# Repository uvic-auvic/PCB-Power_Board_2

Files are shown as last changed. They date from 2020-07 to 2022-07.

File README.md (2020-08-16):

# Power Board 2

## Overview
The Autonomous Underwater Vehicle Interdisciplinary Club (AUVIC) competes in an annual international competition where teams build autonomous underwater vehicles (AUVs) to complete an underwater obstacle course. AUVIC is in need of a new power and battery management board(PMB) for the 2021 Autonomous Underwater Vehicle (AUV).

## Specifications
The new PMB is divided into four subsections. The requirements for each subsection are outlined in the following sections.

### 3.1	Battery Management
- Should have a input voltage range of 18V to 28V.
- Should use two 6 cell LiPo batteries as its power source.
- Should have the ability to run the two batteries in parallel.
- Each battery should have fuses. Regular sized automotive fuses are recommended.
- Should have LEDs to indicate if the battery is connected.
- Should have the ability to monitor battery pack voltage, individual cell voltage and pack current.

### 3.2	Power Distribution
- Should have the following power outputs for external systems:
  - 5V at 8A.
    - LCD board - 4A*
    - Inertial Measurement Unit (IMU) - 500mA
    - Hydrophones - 250mA*
    - Torpedo 5V electronics - 250mA*
    - Motor controller 5V electronics - 250mA*
    - Buffer for unplanned boards - 2.75A
  - 12V at 8A.
    - Doppler Velocity Log (DVL) - 3A
    - Ball dropper and grabber arm - 3A*
    - Buffer for unplanned boards - 2A
  - 16V at 3A.
    - Nvidia Jetson TX2 and peripherals - 3A
  - VBatt (22.2V nominal) at 60A continuous.
    - Motor controller - 60A peak
    - Torpedo launcher - 30A for < 1s
- Should be able to switch on/off all external power using the microcontroller.
- Should have the ability to monitor current for each external power output.
- Should have LEDs at each output to indicate if the output is on or off.
- Should have fuses at each output. Regular sized automotive fuses are recommended.

\* = Estimated values.

### 3.3	Microcontroller & Communication
- Should use a STM32F413 microcontroller. 
- Should have a RS232 transceiver to communicate with an IMU.
- Should have LEDs connected to the microcontroller for debugging and to show system status.
- Should use a Controller Area Network (CAN) bus to communicate to external systems.

### 3.4	Sensors
- Should connect to a reed switch to power on/off the AUV.
- Should connect to a water sensor to detect leaks in the vehicle’s housing.
- Should measure internal pressure, temperature, and humidity.
- Should connect to an external water pressure sensor used to determine the AUV’s depth in the water.

## Progress
Schematic completed

Simulations completed

Layout in progress

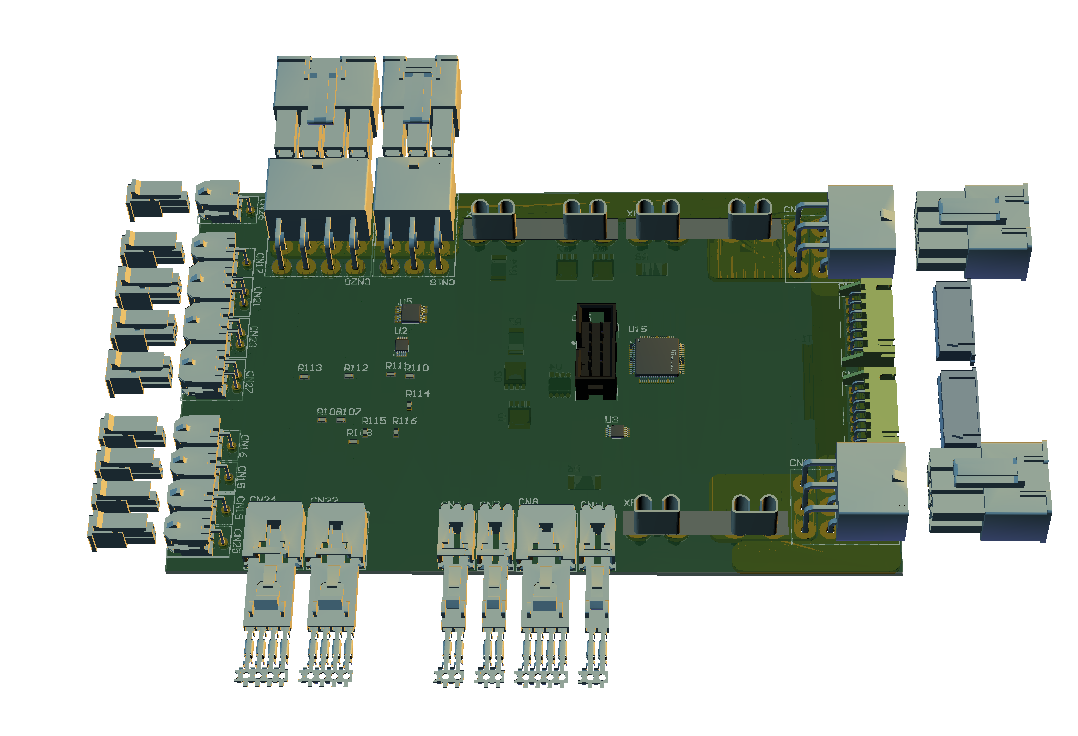
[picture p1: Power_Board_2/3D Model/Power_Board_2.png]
Image of layout thus far


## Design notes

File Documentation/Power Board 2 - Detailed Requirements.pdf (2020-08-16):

## Overview

The Autonomous Underwater Vehicle Interdisciplinary Club (AUVIC) competes in an annual international competition where teams build autonomous underwater vehicles (AUVs) to complete an underwater obstacle course. AUVIC is in need of a new power and battery management board(PMB) for the 2021 Autonomous Underwater Vehicle (AUV).

## Specifications

The new PMB is divided into four subsections. The requirements for each subsection are outlined in the following sections.

## 3.1 Battery Management

The following specifications were established by AUVIC for the battery management section of the power board:
1. Should have a input voltage range of 18V to 28V.
2. Should use two 6 cell LiPo batteries as its power source.
3. Should have the ability to run the two batteries in parallel.
4. Each battery should have fuses. Regular sized automotive fuses are recommended.
5. Should have LEDs to indicate if the battery is connected.
6. Should have the ability to monitor battery pack voltage, individual cell voltage and pack current.

## 3.2 Power Distribution

The following specifications were provided by AUVIC for the power distribution section of the PMB:
1. Should have the following power outputs for external systems:
1.1. 5V at 8A.
1.1.1. LCD board - 4A*
1.1.2. Inertial Measurement Unit (IMU) - 500mA
1.1.3. Hydrophones - 250mA*
1.1.4. Torpedo 5V electronics - 250mA*
1.1.5. Motor controller 5V electronics - 250mA*
1.1.6. Buffer for unplanned boards - 2.75A
1.2. 12V at 8A.
1.2.1. Doppler Velocity Log (DVL) - 3A
1.2.2. Ball dropper and grabber arm - 3A*
1.2.3. Buffer for unplanned boards - 2A
1.3. 16V at 3A.
1.3.1. Nvidia Jetson TX2 and peripherals - 3A
1.4. VBatt (22.2V nominal) at 60A continuous.

1

1.4.1. Motor controller - 60A peak
1.4.2. Torpedo launcher - 30A for < 1s
2. Should be able to switch on/off all external power using the microcontroller.
3. Should have the ability to monitor current for each external power output.
4. Should have LEDs at each output to indicate if the output is on or off.
5. Should have fuses at each output. Regular sized automotive fuses are recommended.
* Estimated values.

## 3.3 Microcontroller & Communication

The following specifications were provided by AUVIC for the microcontroller and communication section of the power board:
1. Should use a STM32F413 microcontroller.
2. Should have a RS232 transceiver to communicate with an IMU.
3. Should have LEDs connected to the microcontroller for debugging and to show system status.
4. Should use a Controller Area Network (CAN) bus to communicate to external systems.

## 3.4 Sensors

From AUVIC, the following requirements were given for the sensors section of the power board:
1. Should connect to a reed switch to power on/off the AUV.
2. Should connect to a water sensor to detect leaks in the vehicle’s housing.
3. Should measure internal pressure, temperature, and humidity.
4. Should connect to an external water pressure sensor used to determine the AUV’s depth in the water.

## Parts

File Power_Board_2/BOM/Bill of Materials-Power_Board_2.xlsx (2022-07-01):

Line # | Name | Description | Designator | Quantity | Manufacturer 1 | Manufacturer Part Number 1 | Manufacturer Lifecycle 1 | Supplier 1 | Supplier Part Number 1 | Supplier Unit Price 1 | Supplier Subtotal 1
 | CL10B104JB8NNNC | CAP CER 0.1UF 50V X7R 0603 | C1, C2, C3, C4, C5, C6, C8, C16, C22, C23, C32, C38, C39, C41, C42, C47, C49, C50, C51, C53, C60, C64, C66, C67, C68, C69, C70, C71, C74, C75, C76, C77, C78, C79, C80, C81, C82, C83, C84, C85, C86, C87, C88, C89 | 44
 | CL31B106KBHNNNE | Cap Ceramic 10uF 50V X7R 10% Pad SMD 1206 125°C T/R | C7, C24, C25, C26, C27, C40, C46, C52, C72 | 9
 | CL31B475KBHNNNE | Capacitor 4.7 uF 50 VDC PU=2000 ST, CL31B475KBHNNNE, Samsung | C9, C10, C21, C37 | 4 | Samsung | CL31B475KBHNNNE | Volume Production | Digi-Key | 1276-2789-1-ND | 0.38374 | 1.53
 | 470nF, 50V, 10%, 0603, Ceramic, SMD | Capacitor, Ceramic, 50V, 10%, 0603 SMD, X7R | C11, C28 | 2 | TDK | C1608X7R1H474K080AC | Volume Production | Digi-Key | 445-5952-6-ND | 0.26256 | 0.52512
 | CL10B102KB8NNNC | Cap Ceramic 0.001uF 50V X7R 10% Pad SMD 0603 125°C T/R | C12, C18, C29 | 3
 | GRM188R60J226MEA0D | MURATA - GRM188R60J226MEA0D - SMD Multilayer Ceramic Capacitor, 22 µF, 6.3 V, 0603 [1608 Metric], ± 20%, X5R, GRM Series | C13, C14, C19, C20 | 4
 | CL10C101FB8NNNC | Ceramic capacitor SMD 0603 100 pF 50 V 1 % | C15 | 1
 | CL21B154KBFNNNG | CAP CER 0.15UF 50V X7R 0805 | C17, C33 | 2
 | GRM1885C2A271JA01D | CAP CER 270PF 100V C0G/NP0 0603 | C30 | 1
 | C3216X5R1E476M160AC | TDK - C3216X5R1E476M160AC - SMD Multilayer Ceramic Capacitor, 47 µF, 25 V, 1206 [3216 Metric], ± 20%, X5R, C Series | C31, C35, C36 | 3
 | CGA4C2C0G1H272J060AA | CAP CER 2700PF 50V C0G 0805 | C34 | 1
 | GRM32ER71E226ME15K | CAP CER 22UF 25V X7R 1210 | C43, C44, C48 | 3
 | CL21B105KBFNNNG | SAMSUNG ELECTRO-MECHANICS - CL21B105KBFNNNG - MLCC CAPACITORS | C45, C65, C73 | 3
15 | 0.015uF 50V 0603 SMD, Ceramic | Capacitor, Ceramic, 50V, +/-10%, 0603 SMD, X7R | C54 | 1
2 | 4.7uF 50V 1206 SMD, Ceramic | Capacitor, Ceramic, 50V, +/- 10%, 1206 SMD, X7R | C55 | 1
5 | 1uF 25V 0603 SMD, Ceramic | Capacitor, Ceramic, 25V, +/- 10%, 0603 SMD, X5R | C56, C57 | 2 | Murata | GRM188R61E105KA12D | Volume Production | Digi-Key | 490-3897-1-ND | 0 | 0
4 | 0.1uF, 50V, 10%, X7R, 1608 | CAP CER 0.1UF 50V 10% X7R 1608 (0603) | C58 | 1 | Samsung | CL10B104KB8SFNC | Volume Production | Digi-Key | 1276-1936-1-ND | 0.10098 | 0.10098
6 | 10uF 10V 0805 SMD, Ceramic | Capacitor, Ceramic, 10V, +/- 10%, 0805 SMD, X5R | C59 | 1 | Murata | GRM219R61A106KE44D | Not Recommended for New Design | Digi-Key | 490-4735-1-ND | 0 | 0
 | 16pF Ceramic 50V 5% 0603 | Cap Ceramic 16pF 50V C0G 5% SMD 0603 125C Paper T/R | C61, C62 | 2
 | 2.2uF, 50V, 0603 SMD, X5R, Ceramic | Capacitor, Ceramic, 50V, 10%, 0603 SMD, X5R | C63 | 1 | Murata | GRM188R61H225KE11D | Volume Production | Digi-Key | 490-10733-6-ND | 0.38374 | 0.38374
 | 76825-0006 | CONNECTOR, HEADER, 6POS, 2ROW, 5.7MM; Product Range:Mega-Fit 76825 Series; Contact Termination Type:Through Hole; Gender:Header; No. of Contacts:6; Pitch Spacing:5.7mm; Contact Plating:Tin Plated Contacts; Contact Material:Copper | CN1, CN2, CN18 | 3 | Molex | 76825-0006 | Volume Production | Digi-Key | WM11971-ND | 2.39 | 7.18
 | S7B-XH-A(LF)(SN) | CONN HEADER XH SIDE 7POS 2.5MM | CN3, CN4 | 2 | JST | S7B-XH-A(LF)(SN) | Volume Production | Digi-Key | 455-2240-ND | 0.45443 | 0.90886
 | ST Debug Header 10-pin THT | CONN HEADER VERT 10POS 2.54MM | CN5 | 1 | Sullins | SBH11-PBPC-D05-ST-BK | Volume Production | Digi-Key | S9169-ND | 0.42413 | 0.42413
 | 1x2 Shrouded Right Angle | 02 MTE HDR SRRA LATCH | CN6, CN7, CN11 | 3 | TE Connectivity | 5-104935-5 | Volume Production | Digi-Key | A33855-ND | 1.47 | 4.42
 | Header, Male, 1x4, RA, Pitch 0.1" (2.54mm) | Connector Header Through Hole, Right Angle 4 position 0.100" (2.54mm) | CN8, CN22, CN24 | 3 | TE Connectivity | 5-104935-1 | Volume Production | Digi-Key | A33860-ND | 1.65 | 4.94
 | Header, Female, 1x2, Right Angle, Pitch 0.118" (3.00mm), THT | Connector Header Through Hole, Right Angle 2 position | CN15, CN16, CN17, CN19, CN25, CN26 | 6 | Molex | 43045-0202 | Volume Production | Digi-Key | WM1819-ND | 1.49 | 8.97
 | 76825-0008 | MOLEX 76825-0008. CONNECTOR, HEADER, 8POS, 2ROW, 5.7MM | CN20 | 1 | Molex | 76825-0008 | Volume Production | Digi-Key | WM11972-ND | 2.86 | 2.86
 | Header, Female, 2x2, RIght Angle, Pitch: 0.118" (3.00mm), THT | Connector Header Through Hole, Right Angle 4 position 0.118" (3.00mm) | CN21, CN23, CN27 | 3 | Molex | 0430450402 | Volume Production | Digi-Key | WM1820-ND | 2.26 | 6.79
 | LT Q39G-Q1OO-25-1 | LED GREEN DIFFUSED 0603 SMD | D1, D2, D4, D5, D6, D7, D11, D12, D13, D14 | 10 | Osram Opto | LT Q39G-Q1OO-25-1 | Volume Production | Digi-Key | 475-3442-1-ND | 0.2767 | 2.77
 | LED, 0805 (2012), Orange, Clear | LED, 0805 (2012), Orange, Clear | D3 | 1
17 | RB060M-60TR | Diode, Schottky, 60V, 2A | D8 | 1 | Rohm | RB060M-60TR | Volume Production | Digi-Key | 846-RB060M-60CT-ND | 0.43423 | 0.43423
 | DSS14UTR | Diode, Schottky, 40V, 1A | D9, D10 | 2 | Sangdest Microelectronics | DSS14UTR |  | Digi-Key | 1655-1927-1-ND | 0.15148 | 0.30295
 | LBQ39E-N1OO-35-1 | LED BLUE DIFFUSED 0603 SMD | D15 | 1 | Osram Opto | LBQ39E-N1OO-35-1 | Volume Production | Digi-Key | 475-2815-1-ND | 0.45443 | 0.45443
 | LSQ976-NR-1 | LED Red 645nm 2-Pin Chip 0603(1608Metric) T/R | D16 | 1 | Osram Opto | LSQ976-NR-1 | Volume Production | Digi-Key | 475-2512-1-ND | 0.28276 | 0.28276
 | CUS08F30,H3F | Diode Schottky 30V 800mA Surface Mount USC | D17, D18, D19 | 3 | Toshiba | CUS08F30,H3F | Volume Production | Digi-Key | CUS08F30H3FCT-ND | 0.32315 | 0.96945
 | PESD36VS2UT,215 | TVS DIODE 36V 60V SOT23 | D21, D22 | 2 | Nexperia | PESD36VS2UT,215 |  | Digi-Key | 1727-5397-1-ND | 0.39384 | 0.78768
 | SMD Fuse, 250mA, 63V, 1206 | SMD Fuse, 250mA, 63V, 1206 | F1 | 1 | Bel | C1Q250 | Volume Production | Digi-Key | 507-1073-1-ND | 0.31305 | 0.31305
 | BLM18AG601SN1D | Chip Ferrite Bead for General Use, 600 Ohm, 500 mA, -55 to 125 degC, 1.6 x 0.8 x 0.95 mm SMD, Tape and Reel | FB1 | 1 | Murata | BLM18AG601SN1D | Volume Production | Digi-Key | 490-1014-1-ND | 0.10098 | 0.10098
 | 1x2 Male Header |  | JP1, JP2, JP3, JP4 | 4 | Harwin | M20-9730246 | Volume Production | Digi-Key | 952-3073-ND | 0.11108 | 0.44433
 | SRP1270-2R2M | BOURNS SRP1270-2R2M Surface Mount Power Inductor, SRP1270 Series, 2.2 H, 22 A, 40 A, Shielded, 4200 ohm | L1 | 1 | Bourns | SRP1270-2R2M | Volume Production | Digi-Key | SRP1270-2R2MCT-ND | 1.69 | 1.69
 | PG0936.682NL | Inductor Power Shielded Wirewound 6.8uH/5.4uH 20% 100KHz Ferrite 18A 0.0035Ohm DCR Automotive | L2 | 1 | Pulse | PG0936.682NL | Volume Production | Digi-Key | 553-3159-ND | 3.27 | 3.27
 | 7447709150 | WURTH ELEKTRONIK - 7447709150 - Power Inductor (SMD), 15 µH, 6.5 A, Shielded, 8 A, WE-PD Series, 12mm x 12mm x 10mm | L3 | 1 | Wurth Electronics | 7447709150 | Volume Production | Digi-Key | 732-1242-1-ND | 2.43 | 2.43
16 | NR4018T6R8M | 6.8uH 1.06A | L4 | 1 | Taiyo Yuden | LMNR4018T6R8M |  | Digi-Key | 587-2657-1-ND | 0.41404 | 0.41404
 | Mount_Hole_3mm | Mounting hold for M3 hex standoff | MH1, MH2, MH3, MH4, MH5, MH6 | 6
 | MOSFET N-Channel, 40V, 100A, 272W | MOSFET N-Channel, 40V, 100A, 272W, Enh-Mode | Q1, Q2, Q7, Q8 | 4 | Nexperia | PSMN1R8-40YLC,115 |  | Digi-Key | 1727-1052-1-ND | 1.33 | 5.33
 | IPC50N04S5L5R5ATMA1 | N-CHANNEL_30/40V | Q3, Q4, Q5, Q6 | 4 | Infineon | IPC50N04S5L5R5ATMA1 |  | Digi-Key | IPC50N04S5L5R5ATMA1CT-ND | 0.86846 | 3.47
 | BC856A,215 | PNP 65V 100mA 250mW | Q10 | 1
 | BC846B,215 | NPN 65V 100mA 250mW | Q11, Q12, Q13, Q14, Q15 | 5
 | CRCW06036K34FKEA | VISHAY CRCW06036K34FKEA. SMD Chip Resistor, Thick Film, 6.34 kohm, 75 V, 0603 [1608 Metric], 100 mW, 1%, CRCW Series | R2, R3, R75, R86 | 4
 | ERJ3EKF10R0V | PANASONIC - ERJ3EKF10R0V - SMD Chip Resistor, 0603 [1608 Metric], 10 ohm, ERJ3EK Series, 75 V, Thick Film, 100 mW | R4, R5, R15, R16, R17, R18, R49, R50, R60, R61, R69, R70, R76, R77 | 14
 | HCS2512FTL300 | 300 µOhms ±1% 3W Chip Resistor 2512 (6432 Metric) Automotive AEC-Q200, Current Sense, Moisture Resistant Metal Element | R6, R7, R8, R74 | 4 | Stackpole Electronics | HCS2512FTL300 | Volume Production | Digi-Key | HCS2512FTL300CT-ND | 1.23 | 4.93
 | RC0603FR-0710KL | Res General Purpose Thick Film 0603 10K Ohm 1% 1/10W ±100ppm/°C Molded SMD Paper T/R | R9, R10, R11, R12, R13, R14, R30, R31, R32, R33, R34, R35, R36, R44, R52, R55, R63, R71, R94, R108, R113, R114, R115, R116, R117, R118, R119, R120, R121, R122 | 30
 | ERJ-3EKF5231V | GLOVE, POLYAMIDE, L/FREE, PU, SIZE 6 - More Details | R19, R37 | 2
 | ERJ-3EKF2102V | RESISTOR, 0603, 21K 1%, 0.1W | R20, R38 | 2
 | ERJ3EKF3652V | PANASONIC - ERJ3EKF3652V - SMD Chip Resistor, 0603 [1608 Metric], 36.5 kohm, ERJ3EK Series, 75 V, Thick Film, 100 mW | R21, R39 | 2
 | ERJ-3EKF5232V | ICK FILM, RESISTOR, 52.3KOHM, 100mW, ±1%; Product Range:PANASONIC - ERJ Series; Resistance:52.3kohm; Power Rating:100mW; Resistance Tolerance:± 1%; Resistor Case Style:0603 ^1608 Metric]; Resistor Element Type:Thick Film; MSL:- | R22, R40 | 2
 | ERJ-3EKF6652V | SISTOR, THICK FILM, 66.5KOHM, 100mW,1%; Product Range:PANASONIC - ERJ Series; Resistance:66.5kohm; Power Rating:100mW; Resistance Tolerance:± 1%; Resistor Case Style:0603 ^1608 Metric]; Resistor Element Type:Thick Film; MSL:- | R23, R41 | 2
 | ERJ-3EKF8252V | RES SMD 82.5K OHM 1% 1/10W 0603 | R24, R42 | 2
 | 20.5 Ohm, 1%, 1/10W , 0603, SMD | 20.5 Ohm, 1%, 1/10W , 0603, SMD | R25, R26, R78, R79 | 4 | Panasonic | ERJ3EKF20R5V | Volume Production | Digi-Key | P20.5HCT-ND | 0.03433 | 0.34335
 | 715R, 1%, 1/10W, 0603, SMD | 715R, 1%, 1/10W, 0603, SMD | R27 | 1 | Vishay | CRCW0603715RFKEA | Volume Production | Digi-Key | 541-715HCT-ND | 0.10098 | 0.10098
 | ERJ-3EKF5360V | SMD Chip Resistor, 0603 [1608 Metric], 536 ohm, ERJ3EK Series, 75 V, Thick Film, 100 mW | R43, R84 | 2
 | CSR1206-0R002F1 | RES 0.002 OHM 1W 1% 1206 | R45, R56, R67 | 3 | Riedon | CSR1206-0R002F1 | Volume Production | Digi-Key | 696-1370-1-ND | 0.59581 | 1.79
 | CRCW060344K2FKEA | Res Thick Film 0603 44.2K Ohm 1% 0.1W(1/10W) ±100ppm/C Pad SMD Automotive T/R | R46 | 1
 | CRCW06031K30FKEA | Res Thick Film 0603 1.3K Ohm 1% 1/10W 100ppm/C Molded SMD SMD Paper T/R | R47, R58 | 2
 | CRCW06035M49FKEA | RES SMD 5.49M OHM 1% 1/10W 0603 | R48 | 1 | Vishay | CRCW06035M49FKEA | Volume Production | Digi-Key | 541-5.49MHCT-ND | 0.10098 | 0.10098
 | ERJ-3EKF7322V | Res Thick Film 0603 73.2K Ohm 1% 0.1W(1/10W) ±100ppm/C Pad SMD Automotive T/R | R51 | 1
 | RC0603FR-072K26L | RES SMD 2.26K OHM 1% 1/10W 0603 | R54, R95, R96 | 3
 | ERJ-3EKF4123V | GLOVE, POLYAMIDE, L/FREE, PU, SIZE 6 - More Details | R57 | 1
 | CRCW06039M76FKEA | RES SMD 9.76M OHM 1% 1/10W 0603 | R59 | 1
 | ERJ-3EKF1913V | RES, THICK FILM, 191KOHM, 0.1W, 0603 | R62 | 1
 | ERJ-3EKF3321V | RES SMD 3.32K OHM 1% 1/10W 0603 | R66 | 1
 | CRCW0603-100KFKEA | Resistor; Thick Film; 100 Kilohms; 0.1 W; 1%; SMT; 0603; TCR 37 ppm/DegC; Tape and Reel | R68, R102, R107, R109, R110, R111, R112 | 7
 | RC0603FR-076K65L | RES SMD 6.65K OHM 1% 1/10W 0603 | R72 | 1
8 | 10kR, 1%, 1/10W, 0603 SMD | 10kR, 1%, 1/10W, 0603 SMD | R80, R87, R89, R91, R92, R97, R98 | 7 | Yageo Phycomp | RC0603FR-0710KL | Volume Production | Digi-Key | 311-10.0KHRDKR-ND | 0.02222 | 0.22217
7 | 3.9k, 5%, 1/8W, 0805 SMD | 3.9k, 5%, 1/8W, 0805 SMD | R82 | 1 | Stackpole Electronics | RMCF0805JT3K90 | Volume Production | Digi-Key | RMCF0805JT3K90DKR-ND | 0.10098 | 0.10098
10 | 680, 5%, 1/8W, 0805 SMD | 680, 5%, 1/8W, 0805 SMD | R83 | 1 | Stackpole Electronics | RMCF0805JT680R | Volume Production | Digi-Key | RMCF0805JT680RDKR-ND | 0.10098 | 0.10098
 | RC0603FR-07110RL | RES SMD 110 OHM 1% 1/10W 0603 | R85, R88, R90 | 3
 | CRCW0603330RFKEA | Res Thick Film 0603 330 Ohm 1% 0.1W(1/10W) +/-100ppm/ßC Pad SMD Automotive T/R | R93 | 1
 | RC0603FR-0733RL | Res Thick Film 0603 33 Ohm 1% 1/10W +/-100ppm/ßC Molded SMD Paper T/R | R99, R101 | 2
 | RC0603FR-07120RL | Res Thick Film 0603 120 Ohm 1% 0.1W(1/10W) ±100ppm/C Epoxy SMD T/R | R100 | 1
 | ERJ3EKF1001V | Res Thick Film 0603 1K Ohm 1% 1/10W ±100ppm/°C Molded SMD Punched Carrier T/R | R104 | 1
 | PTS645SL43SMTR92LFS | Black Switch Tactile N.O. SPST Round Button Gull Wing 0.05A 12VDC 100000Cycles 1.27N SMD T/R | SW1 | 1 | ITT C&K | PTS645SL43SMTR92LFS | Volume Production | Digi-Key | CKN10880CT-ND | 0.31305 | 0.31305
 | DPDT, 12V, 200mA, SMT | DPDT, 12V, 200mA, SMT | SW2 | 1 | Nidec Copal | CL-SB-22A-01T | Volume Production | Digi-Key | 563-1338-1-ND | 1.08 | 1.08
 | INA226AIDGSR | Bi Directional Current and Power Monitor 10-Pin VSSOP T/R | U1, U2, U3, U6, U8, U10, U11 | 7 | Texas Instruments | INA226AIDGSR | Volume Production | Digi-Key | 296-29034-1-ND | 3.21 | 22.48
 | MIC5014YM-TR | High-Side or Low-Side Gate Driver IC Non-Inverting 8-SOIC | U4, U12 | 2 | Microchip | MIC5014YM-TR | Volume Production | Digi-Key | 576-1233-1-ND | 2.18 | 4.36
13 | LM3150MHX/NOPB | IC REG CTRLR BUCK 14TSSOP | U5, U7 | 2 | TI National Semiconductor | LM3150MHX/NOPB | Volume Production | Digi-Key | 296-35276-1-ND | 3.18 | 6.36
 | BD9E302EFJ-E2 | IC REG BUCK ADJ 3A 8HTSOP-J | U9 | 1
11 | BD9G101G-TR | DC-DC Regulator, 6V-42V in, 1V-29.4V out, 500mA | U13 | 1 | Rohm | BD9G101G-TR | Volume Production | Digi-Key | BD9G101G-CT-ND | 1.5 | 1.5
1 | 3.3V 250mA Linear Reg LDO | IC REG LINEAR 3.3V 250MA SOT23-3 | U14 | 1 | Diodes | AP2138N-3.3TRG1 | Volume Production | Digi-Key | AP2138N-3.3TRG1DICT-ND | 0.48472 | 0.48472
 | STM32F413RGT6 | STMICROELECTRONICS - STM32F413RGT6 - MCU, ARM CORTEX-M4, 100MHZ, LQFP-64 | U15 | 1
 | CD74HC194PWR | IC SHFT REGSTR UNIV BIDIR16TSSOP | U16 | 1 | Texas Instruments | CD74HC194PWR | Volume Production | Digi-Key | 296-12794-1-ND | 0.60591 | 0.60591
 | CAN Transceiver | 1/1 Transceiver Half CANbus 8-SO | U17 | 1 | NXP Semiconductors | TJA1042T/3,118 | Volume Production | Digi-Key | 568-8678-1-ND | 1.32 | 1.32
 | MS560702BA03-50 Pressure Sensor | 1kPa to 120 kPa | U18 | 1
 | Si700XX | I2C Humidity and Temperature Sensor | U19 | 1 | Silicon Labs | SI7021-A20-GM | Volume Production | Digi-Key | 336-3140-5-ND | 3.09 | 3.09
 | ST3232CDR | Dual Transmitter/Receiver RS-232 16-Pin SO T/R | U20 | 1 | STMicroelectronics | ST3232CDR | Volume Production | Digi-Key | 497-3731-1-ND | 1.12 | 1.12
 | Oscillator 8MHz 40ESR | 8Mhz 40ESR 16pF -20°C ~ 70°C | X1 | 1 | Diodes | GC0800044 | Volume Production | Digi-Key | GC0800044CT-ND | 0.60591 | 0.60591
 | 3555-2 | FUSE HOLDER MAXI AUTO BLADE PC | XF1, XF2, XF6 | 3 | Keystone Electronics | 3555-2 | Volume Production | Digi-Key | 36-3555-2-ND | 1.72 | 5.15
 | 3557-2 | Fuse Holder; Auto; 2 in1 Blade; THM; 1 Fuse; Vertical; 30 Amps | XF3, XF4, XF5 | 3

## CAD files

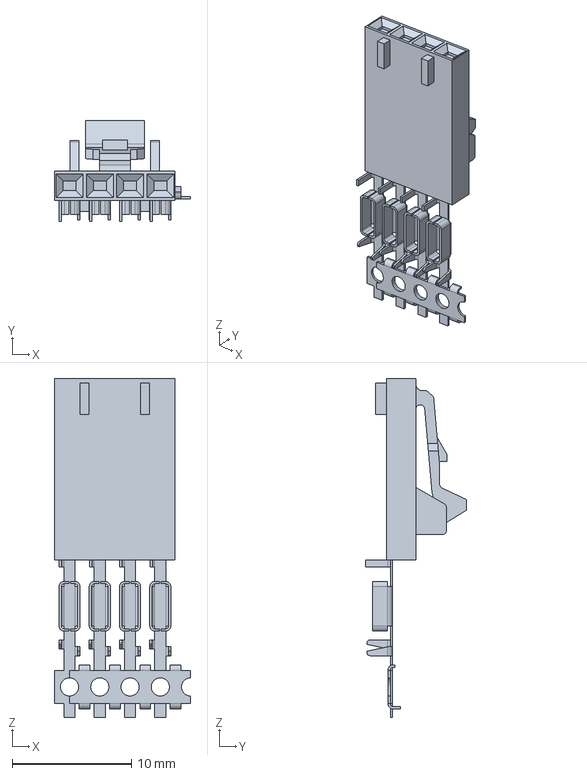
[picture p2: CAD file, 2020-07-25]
Power_Board_2/3D Model/Parts/c-0103961-53-k-3d.stp
11.4 x 8.48 x 28.4 mm

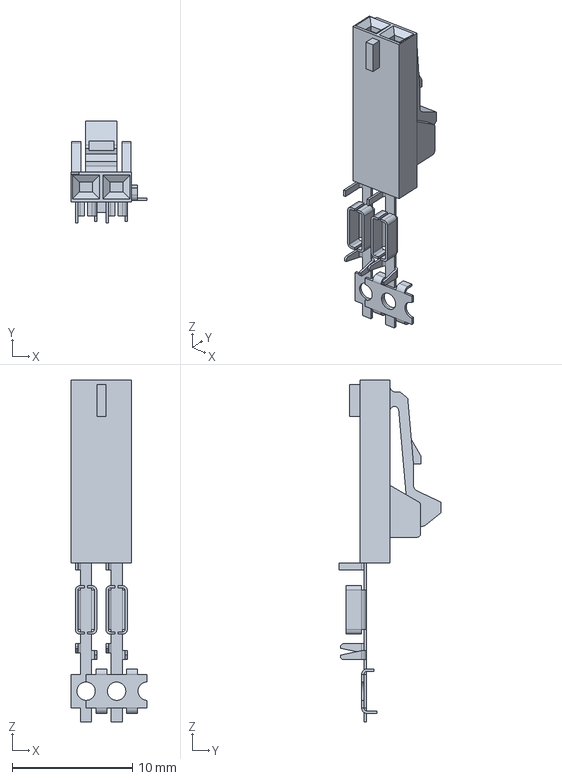
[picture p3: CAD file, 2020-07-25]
Power_Board_2/3D Model/Parts/c-5-103960-1-m-3d.stp
6.35 x 8.48 x 28.4 mm

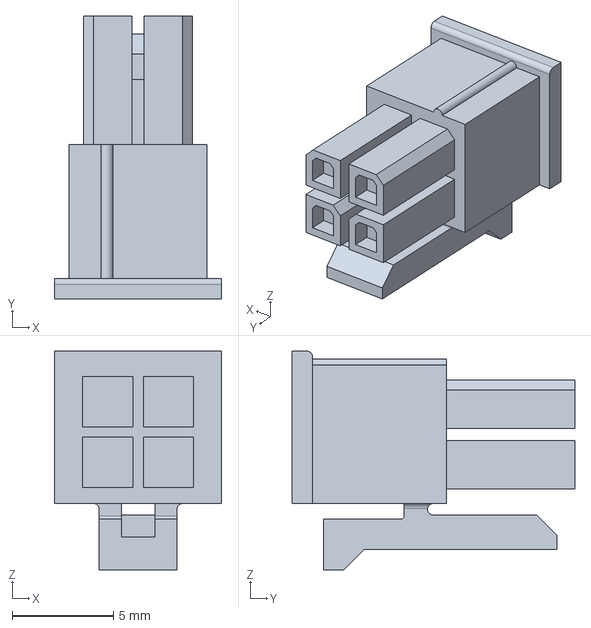
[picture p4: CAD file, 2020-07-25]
Power_Board_2/3D Model/Parts/430250400.stp
8.27 x 14.0 x 10.8 mm

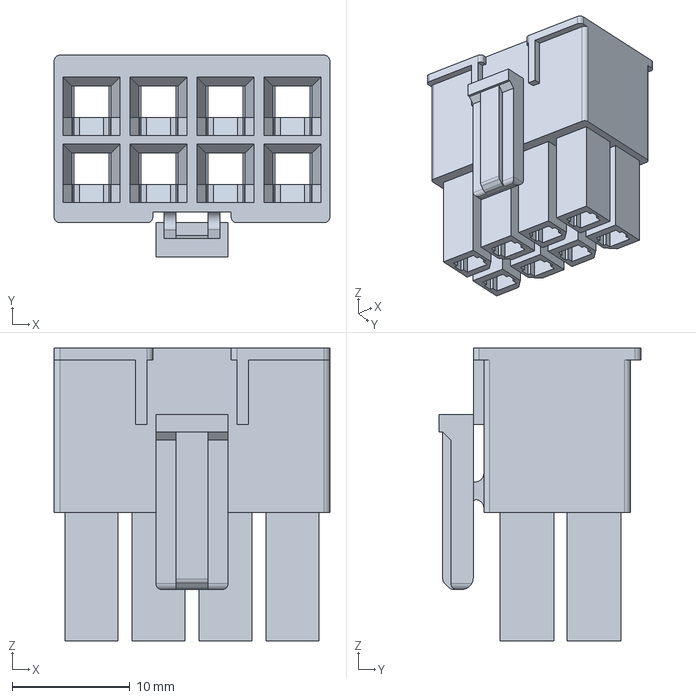
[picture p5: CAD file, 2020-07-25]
Power_Board_2/3D Model/Parts/1716920108.stp
23.4 x 17.2 x 24.9 mm

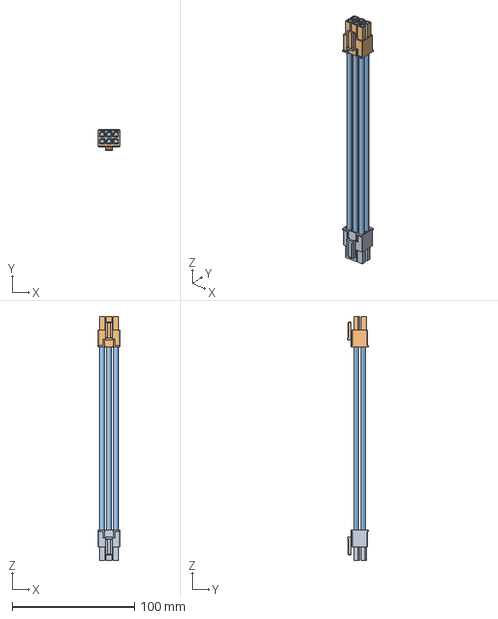
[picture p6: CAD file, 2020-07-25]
Power_Board_2/3D Model/Parts/451360601.stp
17.8 x 17.2 x 199.8 mm

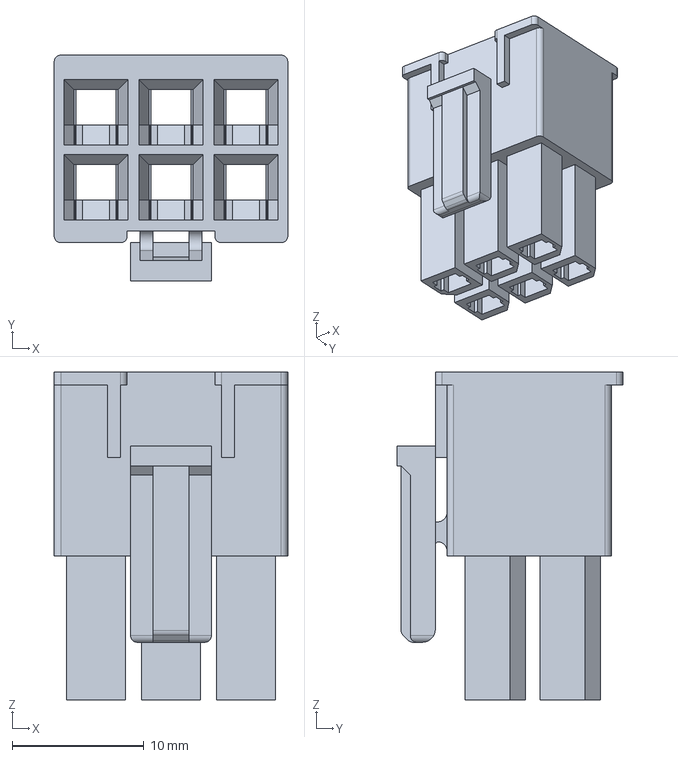
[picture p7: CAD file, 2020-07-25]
Power_Board_2/3D Model/Parts/1700010106.stp
17.8 x 17.2 x 24.9 mm

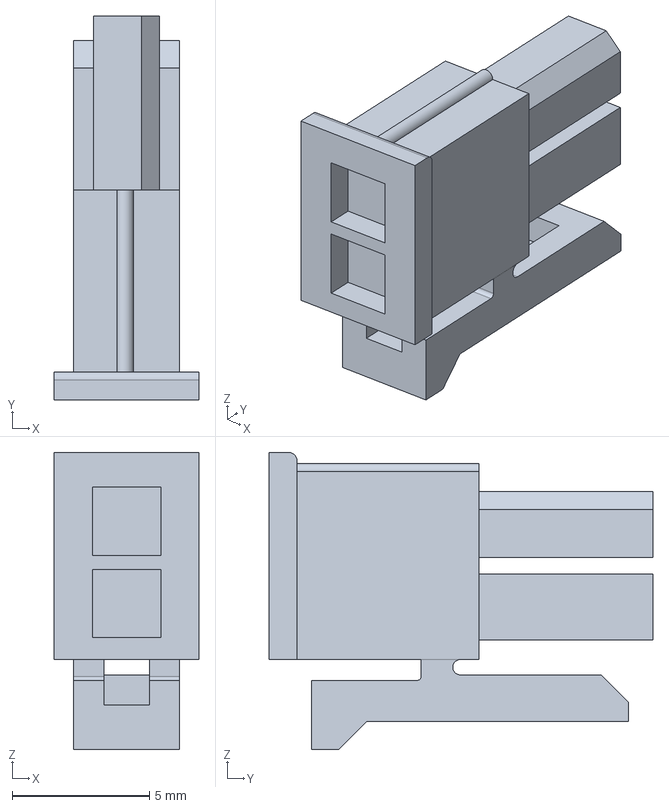
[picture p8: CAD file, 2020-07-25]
Power_Board_2/3D Model/Parts/430250200.stp
5.28 x 14.0 x 10.8 mm

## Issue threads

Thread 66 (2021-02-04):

Power Board 2.0 PCB

rkeen9, 2021-02-04:
## Current Status
- Somebody will do it eventually
- look into splitting it up
## Next Steps
- some signal wires need  rerouting
- micro is not hooked up
- continue development

anijjar, 2023-02-11:
Boards arrived and are being soldered.

Closed 2023-02-11.

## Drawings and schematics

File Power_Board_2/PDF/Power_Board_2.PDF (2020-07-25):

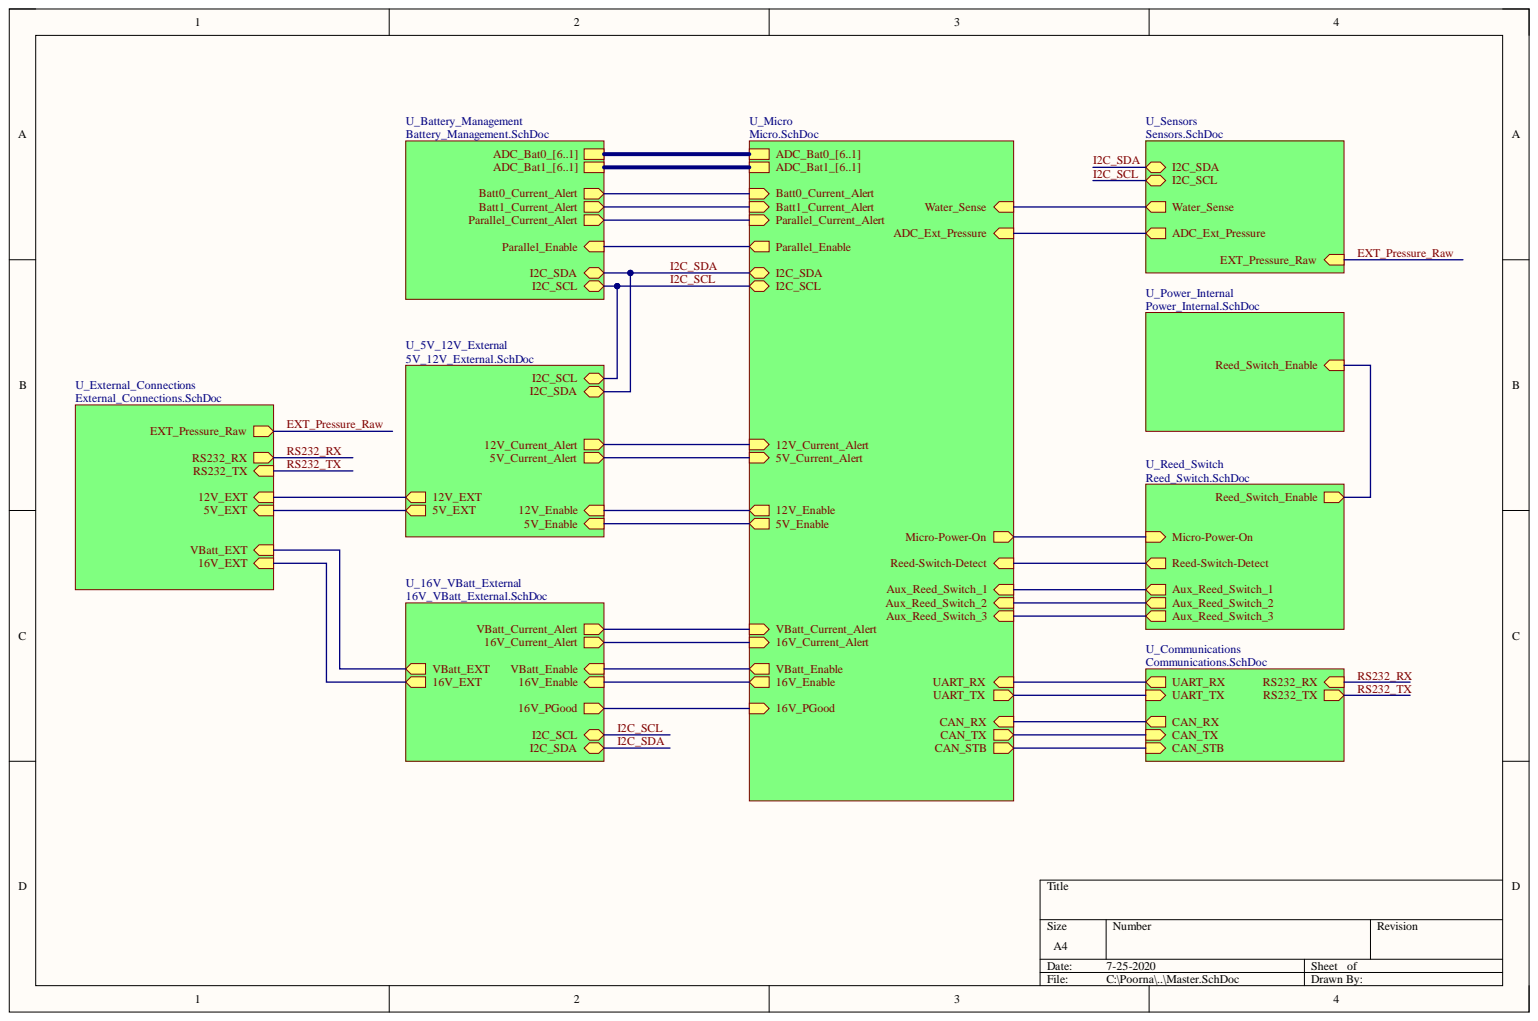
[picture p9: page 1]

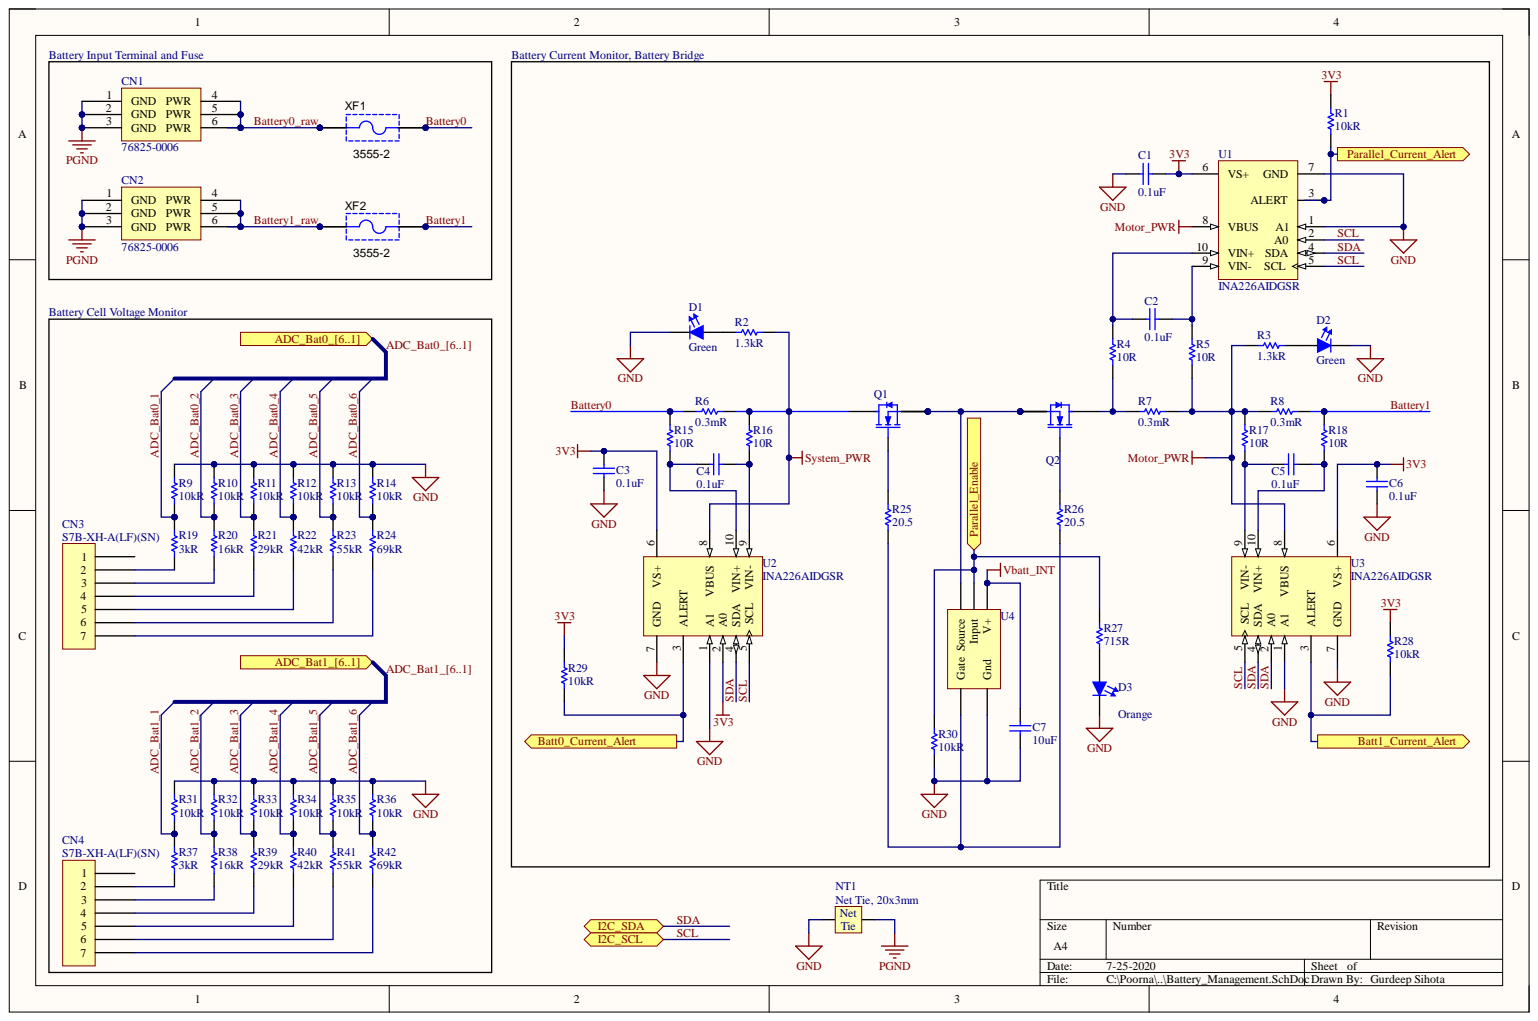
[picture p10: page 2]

Battery Cell Voltage Monitor

GND | C3

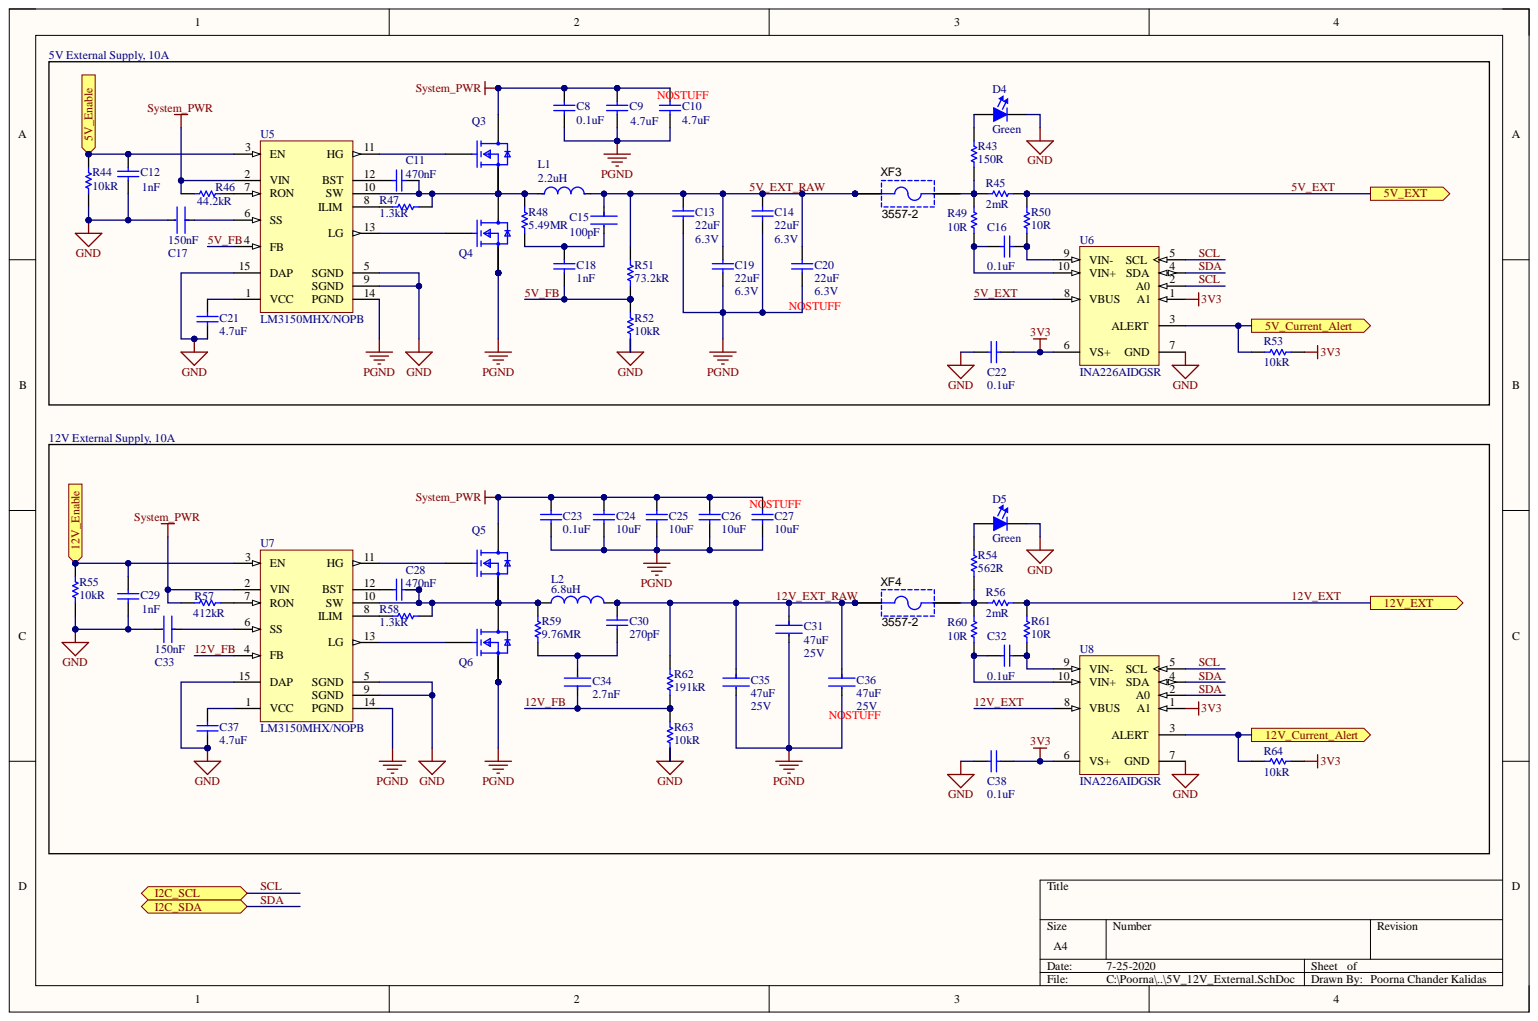
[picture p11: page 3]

VIN 2

R57 | RON 7

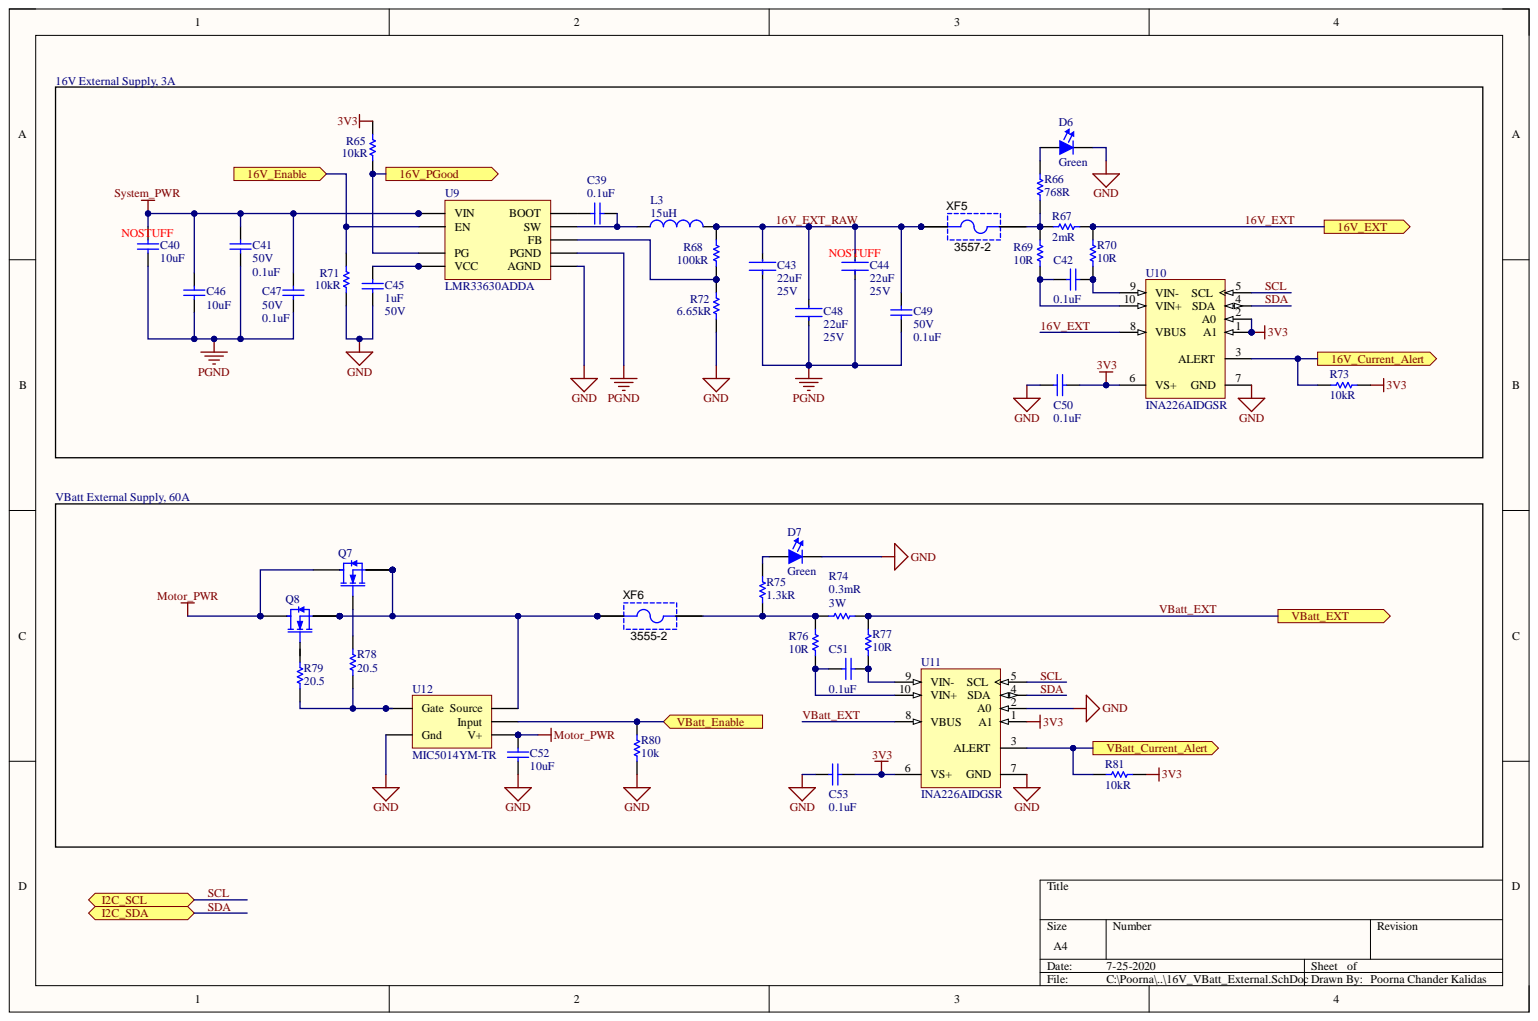
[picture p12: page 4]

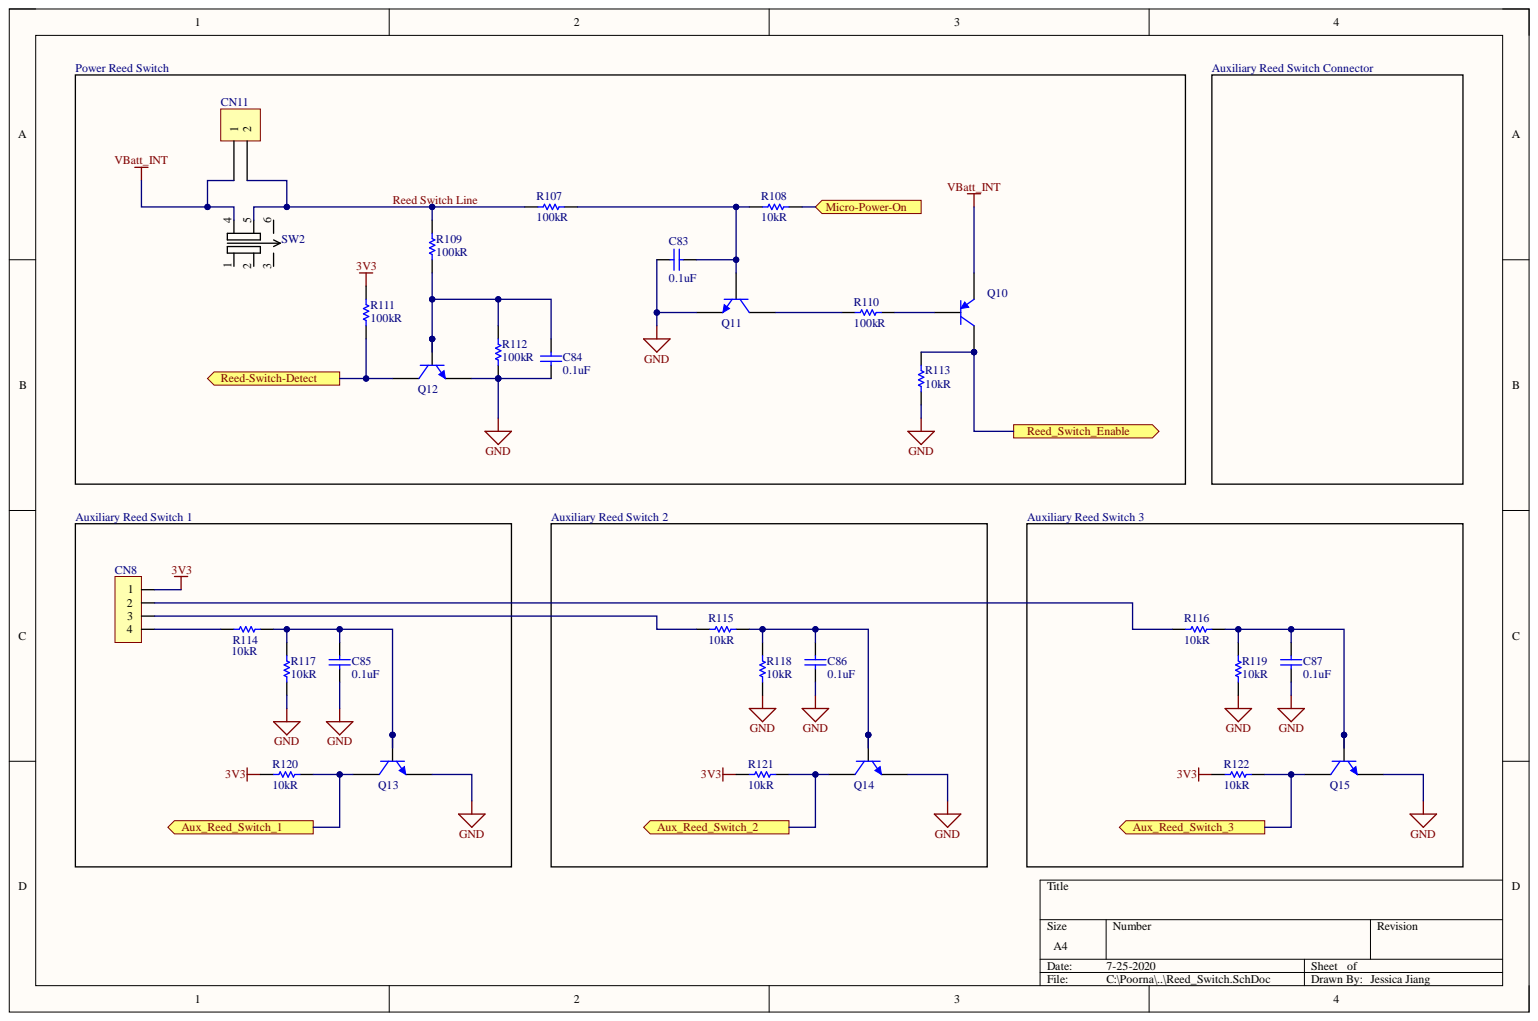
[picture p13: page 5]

Auxiliary Reed Switch Connector

Micro-Power-On Reed Switch Line

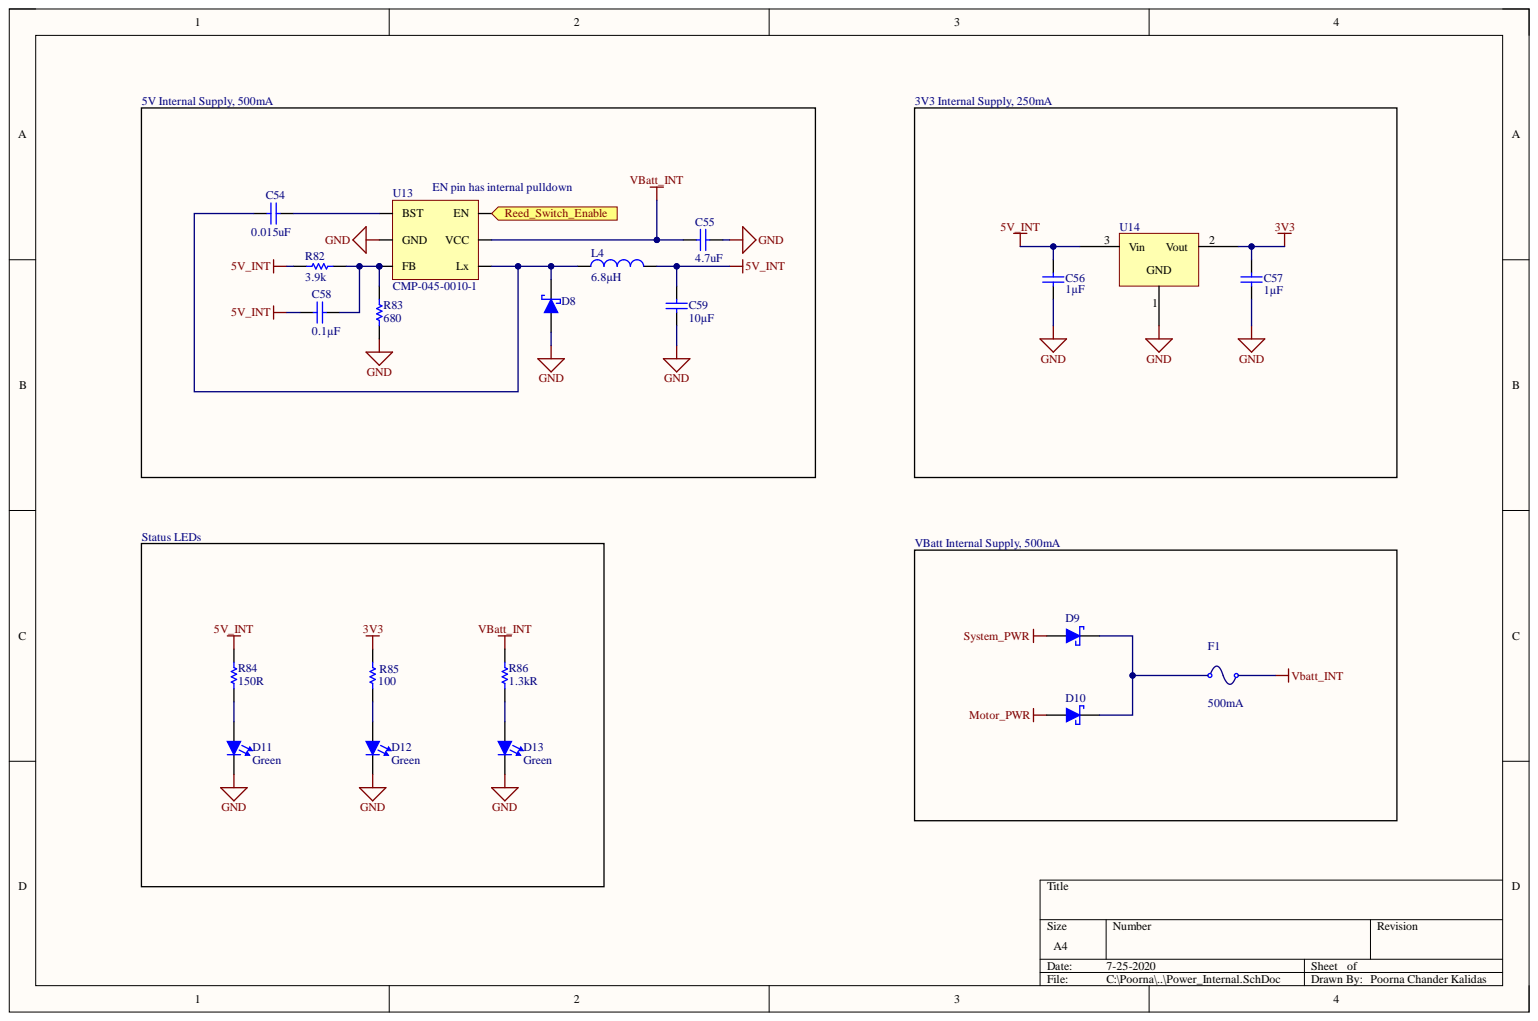
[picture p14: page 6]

VBatt_INT EN pin has internal pulldown

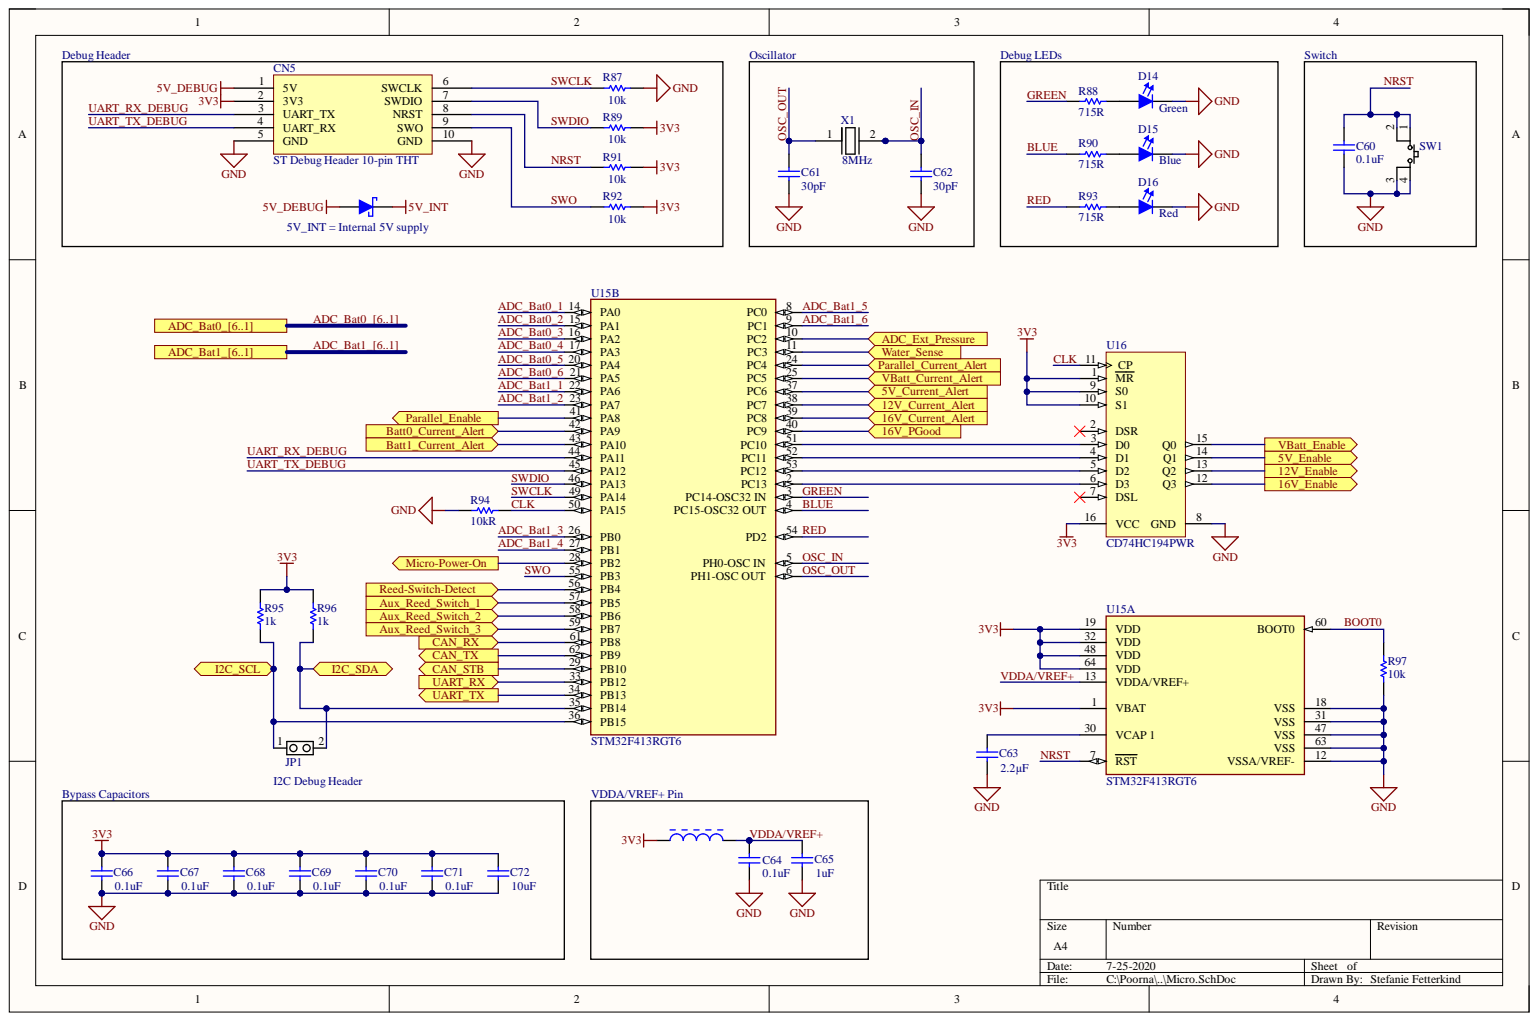
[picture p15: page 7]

ST Debug Header 10-pin THT

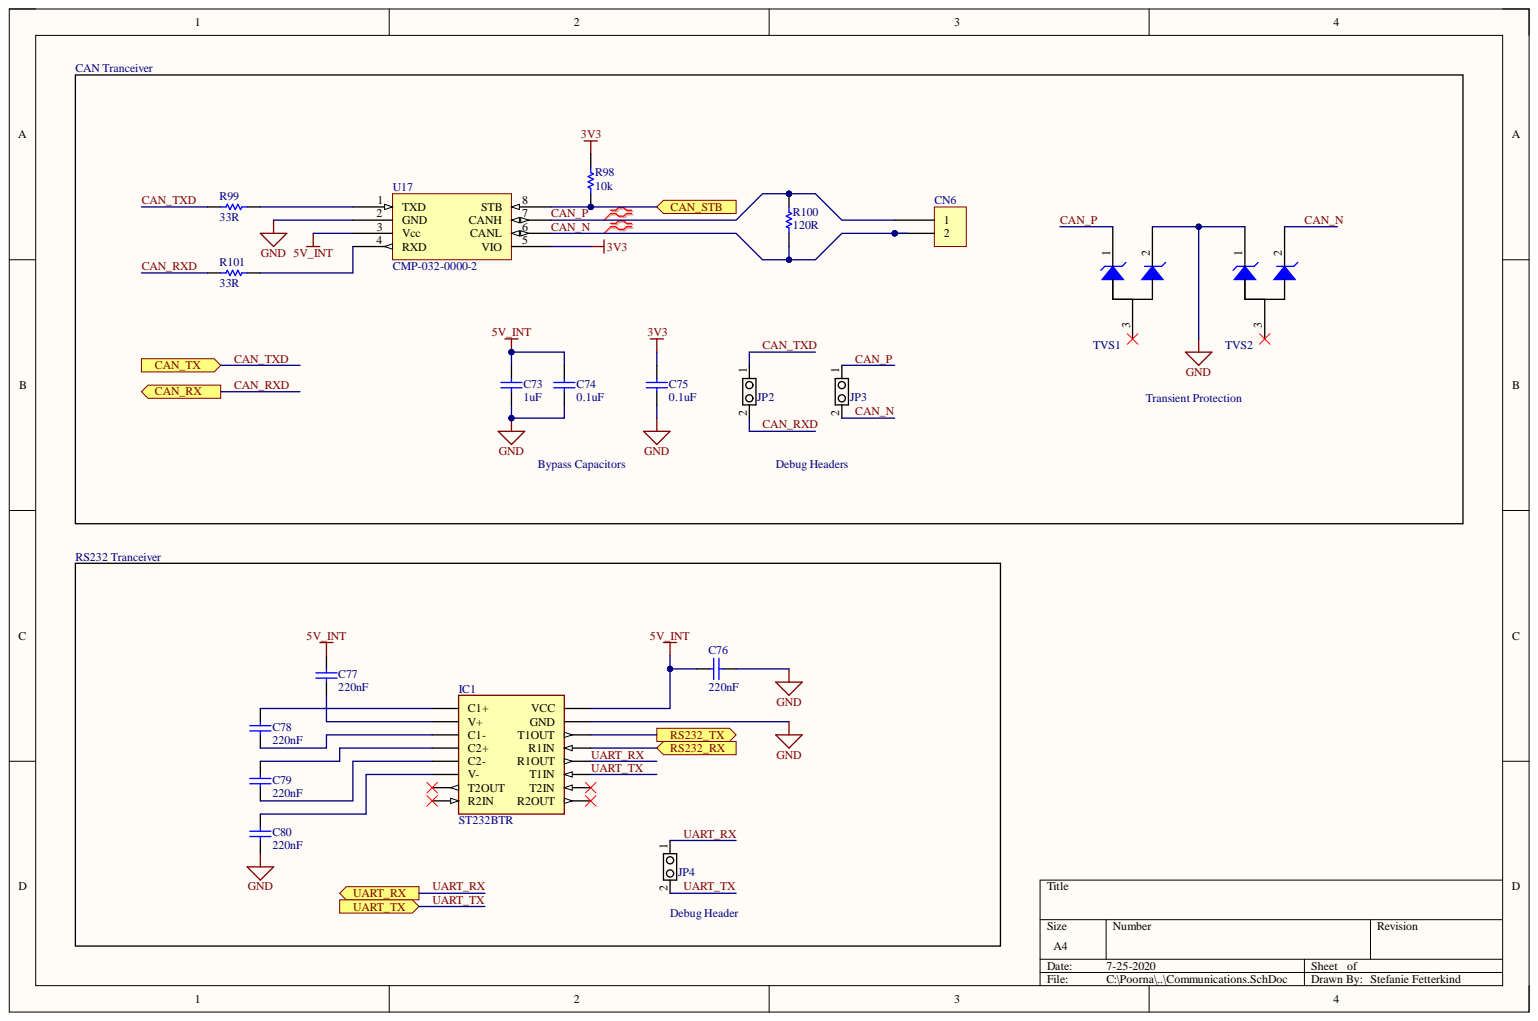
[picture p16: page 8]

C78
220nF

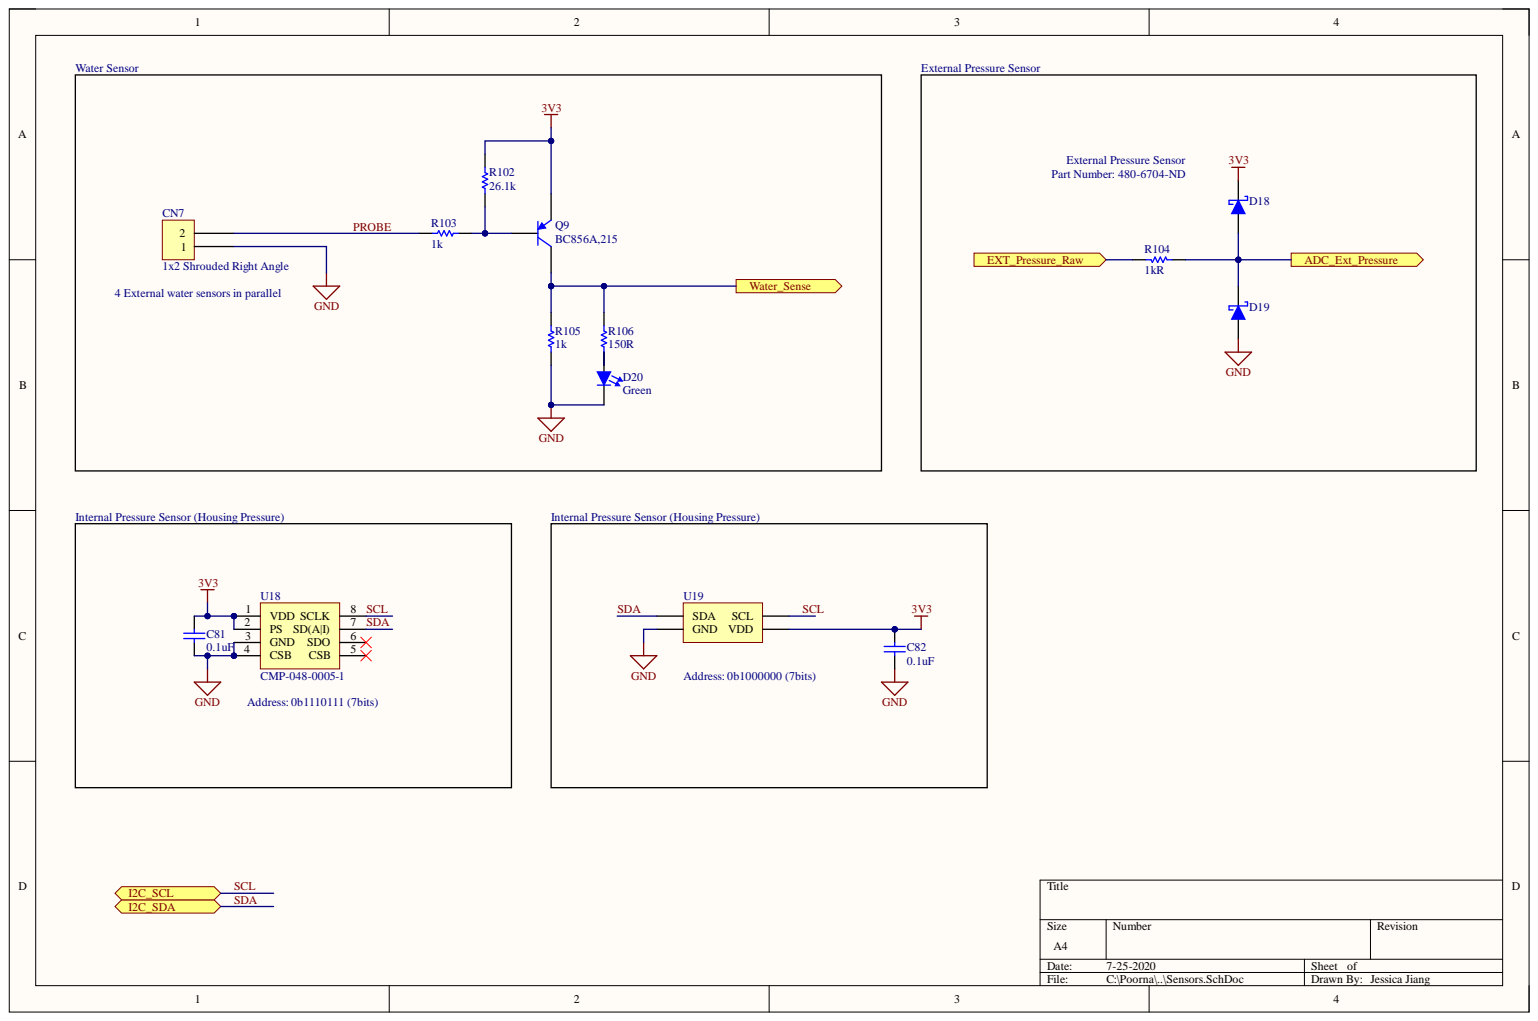
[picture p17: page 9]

4 External water sensors in parallel

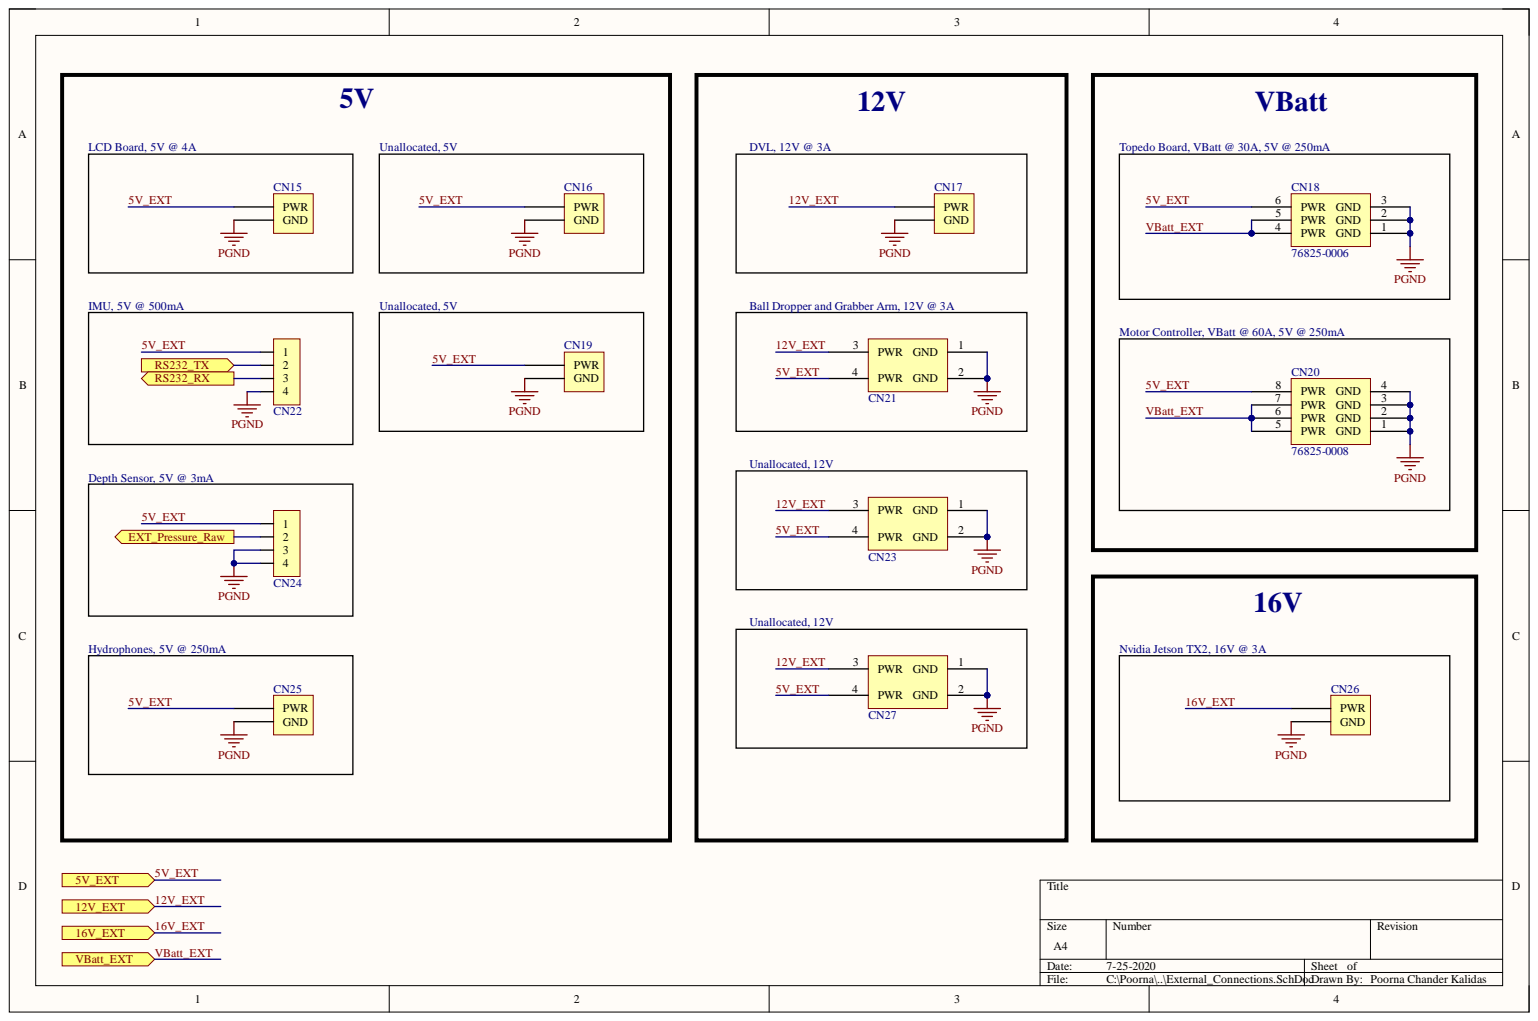
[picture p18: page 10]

Ball Dropper and Grabber Arm, 12V @ 3A

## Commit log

2020-05-14 Made notes on Power External
    [Power_Board_2.PrjPcb, Power_External.SchDoc]
2020-06-27 Added internal 5V and 3.3V rails
    [Power_Board_2.PrjPcb, Power_External.SchDoc, Power_Internal.SchDoc]
2020-06-27 Added Reed Switch Sheet and added ports to master schematic"
    [Master.SchDoc, Power_Board_2.PrjPcb, Power_Internal.SchDoc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]
2020-06-27 Update PDF and BOM
    [Bill of Materials-Power_Board_2.xlsx]
2020-06-29 Started work on 5V buck
    [Power_External.SchDoc]
2020-07-01 TEST TEST TEST
    [Power_External.SchDoc, Power_Internal.SchDoc]
2020-07-02 Added notes based on meeting on July 2 2020
    [Master.SchDoc]
2020-07-08 Removed test message
    [Power_External.SchDoc]
2020-07-08 Poorna (#5)
    * Started work on 5V buck
    * Added notes based on meeting on July 2 2020
    [Master.SchDoc, Power_External.SchDoc, Power_Internal.SchDoc]
2020-07-10 WIP:5V Buck
    [5V_buck.xlsx, Power_External.SchDoc, Power_Internal.SchDoc]
2020-07-11 5V External Buck Done (#7)
    [5V_buck.xlsx, Master.SchDoc, Power_External.SchDoc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]
2020-07-11 Battery Managment Update
    [Battery_Management.SchDoc]
2020-07-12 Split power external into two sheets
    [16V_VBatt_External.SchDoc, 5V_12V_External.SchDoc, Master.SchDoc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]
2020-07-12 Removed target printer from PrjPcb file
    [Power_Board_2.PrjPcb]
2020-07-12 WIP: 12V and 16V Bucks
    [16V_VBatt_External.SchDoc, 5V_12V_External.SchDoc]
2020-07-13 Completed 16V Buck
    [16V_VBatt_External.SchDoc, 5V_12V_External.SchDoc, Master.SchDoc]
2020-07-13 VBatt circuit completed
    [16V_VBatt_External.SchDoc]
2020-07-15 Battery Managment Update 2
    [Battery_Management.SchDoc]
2020-07-18 Added External Connections Schematic Sheet (#16)
    * Added External_Connections.SchDoc
    [16V_VBatt_External.SchDoc, 5V_12V_External.SchDoc, External_Connections.SchDoc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]
2020-07-19 updated water sensor schematic.
    [Sensors.SchDoc]
2020-07-19 Updated port name Signal to Water_Sense
    [Sensors.SchDoc]
2020-07-19 Removed Probe port
    [Sensors.SchDoc]
2020-07-19 Updated master with Reed switch detect and micro power on, updated reed switch to include aux reed ports 1,2, and 3
    [Master.SchDoc, Reed_Switch.SchDoc, Sensors.SchDoc]
2020-07-19 updated reed switch detect and micro power on ports
    [Master.SchDoc]
2020-07-19 updated reed switch enable port
    [Reed_Switch.SchDoc]
2020-07-19 Add Batt voltage to master doc (#23)
    * Added batt voltage adc to master doc
    [5V_12V_External.SchDoc, Master.SchDoc]
2020-07-19 Battery Managment Update 3
    [Battery_Management.SchDoc]
2020-07-20 updated ground symbols
    [Reed_Switch.SchDoc, Sensors.SchDoc]
2020-07-20 Micro Updates
    [Micro.SchDoc]
2020-07-20 Completed 12V buck
    [16V_VBatt_External.SchDoc, 5V_12V_External.SchDoc]
2020-07-20 Supplying internal systems with VBatt_INT instead of System_PWR
    [5V_12V_External.SchDoc, Power_Internal.SchDoc]
2020-07-20 Updated schematics and resolved comments
    [Reed_Switch.SchDoc, Sensors.SchDoc]
2020-07-20 Updated Batt voltage Bus
    [Battery_Management.SchDoc, Master.SchDoc]
2020-07-21 Micro changes
    [Micro.SchDoc]
2020-07-21 Added new fuse holder
    [16V_VBatt_External.SchDoc, 5V_12V_External.SchDoc]
2020-07-22 Micro for commenting
    [Micro.SchDoc]
2020-07-22 Recovering Micro.SchDoc from the dead
    [Micro.SchDoc]
2020-07-22 Fixing master mistakes
    [Master.SchDoc]
2020-07-22 Finalizing mirco
    [Micro.SchDoc]
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2020-07-22 Updated sensors doc to include humidity, temperature, internal and external pressure
    [Sensors.SchDoc]
2020-07-22 Final touches to micro/master and adding comm
    [Communications.SchDoc, Master.SchDoc, Micro.SchDoc]
2020-07-22 Battery Managment Update 5
    [Battery_Management.SchDoc]
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2020-07-22 Compiles without errors. Warnings exist
    [5V_12V_External.SchDoc, Battery_Management.SchDoc, Communications.SchDoc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]
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2020-07-23 Fixed floating ground pin
    [16V_VBatt_External.SchDoc]
2020-07-23 Fixed mistake with VBatt_INT
    [Battery_Management.SchDoc, Power_Internal.SchDoc]
2020-07-23 Ready for external review
    [16V_VBatt_External.SchDoc, 5V_12V_External.SchDoc, Battery_Management.SchDoc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]
2020-07-25 Board perimeter for mech tech
    [1700010106.stp, 1716920108.stp, 430250200.stp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]
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2020-08-13 Schematic ready for review. Layout inprogress.
    [16V_VBatt_External.SchDoc, Battery_Management.SchDoc, Communications.SchDoc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]
2020-08-15 Finalized LEDs and LED resistors
    [16V_VBatt_External.SchDoc, 5V_12V_External.SchDoc, Battery_Management.SchDoc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]
2020-08-16 Added water sensor ADC channel
    [Master.SchDoc, Micro.SchDoc, Power_Internal.SchDoc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]
2020-08-16 Finished 16V supply routing
    [16V_VBatt_External.SchDoc, Power_Board_2.PrjPcb]
2020-08-16 12V and 5V shunt routing complete
    [16V_VBatt_External.SchDoc, 5V_12V_External.SchDoc, Battery_Management.SchDoc]
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2020-08-17 Improved 16V supply layout
    [16V_VBatt_External.SchDoc]
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2020-08-20 Added thermal reliefs to power ground plane.
    [Battery_Management.SchDoc, External_Connections.SchDoc]
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2020-09-21 Oscillator capacitance was wrong.
    [Micro.SchDoc]
2020-12-09 Convert all footprints to low density
    [16V_VBatt_External.SchDoc, 5V_12V_External.SchDoc, Battery_Management.SchDoc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]
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2022-06-02 shorted pgnd to gnd
    [16V_VBatt_External.SchDoc, 5V_12V_External.SchDoc, Battery_Management.SchDoc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]
2022-06-09 Minor Changes made during design review
    [Power_Board_2.PrjPcb]
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2022-06-22 fixed drc errors
    [Power_Board_2.PrjPcb]
2022-06-29 Changes made during team meeting
    - changing thermal relief to direct
    [Power_Board_2.PrjPcb]
2022-07-01 generated output files for JLC
    [Bill of Materials-Power_Board_2.xlsx]
2022-07-13 solder mask issue fixed
